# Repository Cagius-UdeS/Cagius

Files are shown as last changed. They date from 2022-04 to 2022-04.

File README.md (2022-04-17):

# Cagius

Cagius est un projet open source ayant pour objectif de concevoir et construire le mécanisme de gestion de la litière pour une cage à petits animaux automatisée et créer un interface programmable pour gérer les cycles de nettoyage.

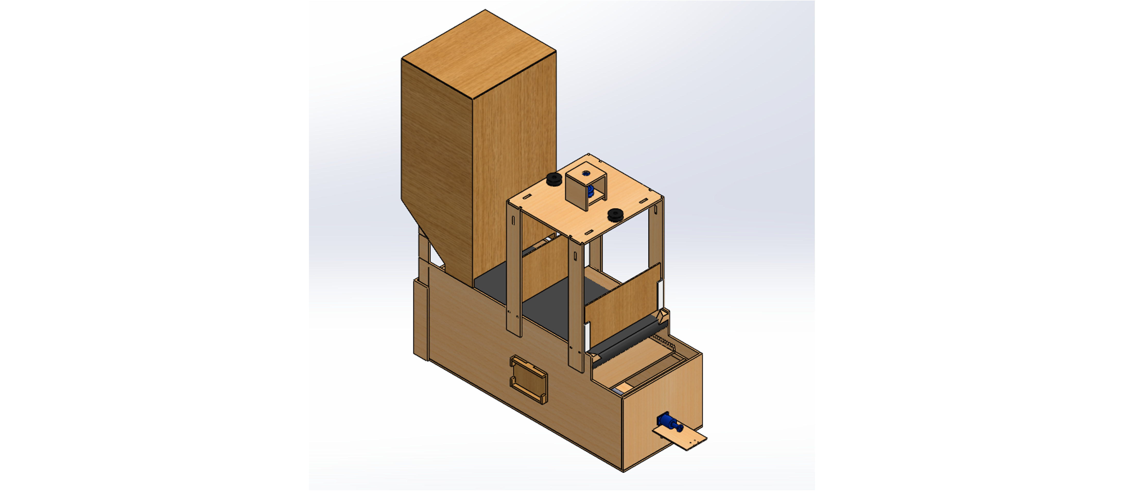
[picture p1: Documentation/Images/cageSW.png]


## Table des matieres

1. [Composantes mécaniques et électroniques](#1-composantes-mécaniques-et-électroniques)
2. [Assemblage](#2-assemblage)
3. [Installation logiciel](#3-installation-logiciel)
4. [Initialisation de la cage](#4-initialisation-de-la-cage)
5. [License](#5-license)

## 1. Composantes mécaniques et électroniques

### 1.1 Composantes mécaniques

- Courroie Synchrone : McMaster **1679K55** 
- Tige Filletée : Mcmaster **98957A154**

### 1.2 Composantes électroniques

- Raspberry Pi 4
- Raspberry Pi Camera
- 2 x Dynamixel XL-430-w250-t
- 2 x Dynamixel XM-430-w350-t
- Module à relais IDUINO - 1 Canal - 5V (ST1080)

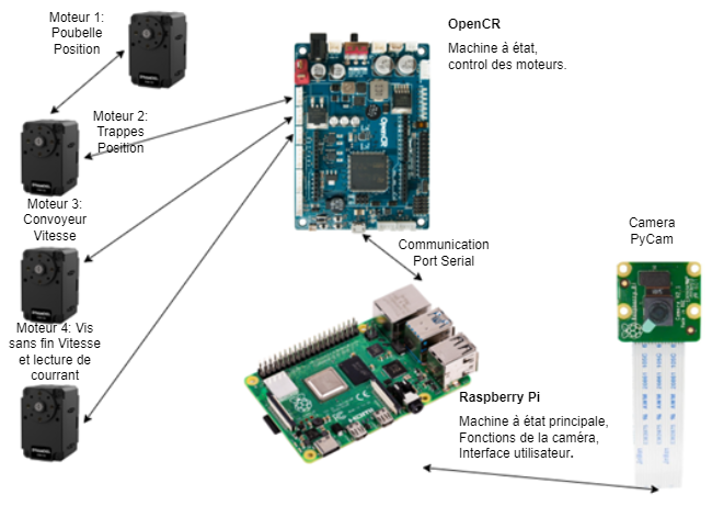
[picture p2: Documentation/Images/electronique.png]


## 2. Assemblage

Pour ce qui est de l'assemblage de la structure de base, il suffit de respecter l'assemblage de la pièce [Poubelle.sldrpt](https://github.com/Cagius-UdeS/Cagius/blob/main/CADs/Poubelle.SLDPRT). En fait, un mélange de colle et de clou à finition a été utilisé pour avoir une structure solide. De plus, le prototype actuelle est fait avec des planches de bois 1/4" découpées au laser et assemblées par la suite.

Pour ce qui est de l'assemblage du convoyeur, des tubes de PVC de 1" ont été utilisé, accompagnés d'adaptateurs imprimés en 3D pour les assembler avec la cage et le moteur. De plus, des bandes élastiques d'entrainements sont utilisées comme courroie pour transmettre le mouvement d'une poulie à l'autre.

[Pour les détails concernants les CADs et leurs pertinences](https://github.com/Cagius-UdeS/Cagius/blob/main/Documentation/Hierarchie_pieces.md)

## 3. Installation logiciel

La section suivante couvre l'installation des logiciels et des librairies nécessaires à la compilation du code.

### 3.1 Installation sur ordinateur

Il est nécessaire de compiler et d'envoyer le code à la carte OpenCR à partir d'un ordinateur, car le Raspberry Pi ne prend pas en charge les librairies de la carte OpenCR et des moteurs Dynamixel.

#### 3.1.1 Installation de Arduino IDE

Afin d'installer Arduino IDE et les librairies nécessaires pour coder les moteurs, il suffit de suivre les étapes suivantes :

1. Télécharger l'application Arduino IDE [ici](https://www.arduino.cc/en/software)
2. Ouvrir l'application et se rendre dans *Fichier*, puis *Préférences*
3. Dans la section *URL de gestionnaire de cartes supplémentaires*, rajouter la ligne suivante:
	`https://raw.githubusercontent.com/ROBOTIS-GIT/OpenCR/master/arduino/opencr_release/package_opencr_index.json`
4. Confirmer les changements en pressant *OK* dans le bas à droite de l'écran.
5. Enfin, installer les librairies Motorcontrole dans la section *Outils* puis *Type de carte* et *Gestionnaire de carte*. Taper OpenCR dans la barre de recherche et installer les librairies.

#### 3.1.2 Installation des librairies pour OpenCR

Afin de pouvoir compiler le code de la carte OpenCR, il est nécessaire d'installer quelques librairies selon les étapes suivantes :

1. Ouvrir l'application Arduino IDE et se rendre dans *Croquis*, puis *Inclure une bibliothèque* et sélectionner *Gestionnaires de bibliothèques*

2. Rentrer *Dynamixel* dans la barre de recherche

3. Installer les libraires

### 3.2 Installation sur Raspberry Pi

Le Raspberry Pi agit comme le cerveau de la cage. En effet, le Raspberry Pi analyse la caméra et l'interface utilisateur.

#### 3.2.1 Installation de Qt designer

Si vous voulez modifier l'interface utilisateur (modifier les fichiers .ui), vous devez télécharger Qt 5 Designer, qui fait parti de Qt Creator. Pour cela, éxecutez les lignes de commandes suivantes dans le terminal :

  ```
  $ sudo apt-get install qttools5-dev-tools
  $ sudo apt-get install qttools5-dev
  ```

#### 3.2.2 Installation de PyQt

Pour concevoir le HMI, nous avons utilisé PyQt qui est un module libre permettant de lier le langage Python avec la bibliothèque Qt. 
L'installation se fait sur le Raspberry Pi et consiste à faire rouler la ligne de commande suivante :

	$ sudo apt-get install python3-pyqt5

Si votre Rapsberry Pi n'est pas à jour, rouler ces lignes de commande au préalable :

	$ sudo apt-get update
	$ sudo apt-get upgrade

À partir de là, pour coder l'interphace graphique on utilise Qt 5 Designer avec le PyQt intégré.

#### 3.2.3 Installation des librairies Open CV

Afin d'installer les librairies OpenCV sur votre Raspberry Pi, 
il suffit de suivre le guide **Setting Up Open-CV for Object Detection** sur ce site:
[Guide d'installation OpenCV](https://core-electronics.com.au/tutorials/object-identify-raspberry-pi.html)

## 4. Initialisation de la cage

Les differents dossiers de code et où les compiler se retrouve [ici](Code/README.md).

Les étapes pour initialiser la cage et la lancer sont les suivantes :

- Remplir le réservoir de litière
- Si premier cycle d'utilisation, mettre une couche de litière sur le convoyeur
- S'assurer que la carte OpenCR, le Raspberry et les bandes LED sont alimentés
- S'assurer que la caméra est branchée sur le Raspberry Pi
- S'assurer que tous les moteurs sont branchés à la carte OpenCR
- Compiler le programme *[userInterface](Code/PyQt/userInterface.py)* sur le Raspberry Pi et attendre que l'initialisation soit complétée et que la fenêtre s'ouvre
- Indiquer le nombre d'animaux présents dans la cage, rentrer les heures d'activités souhaitées de la cage et appuyer sur le bouton **Lancement**
- La cage est prête à être utilisée !

<ins><b>Notez bien</b></ins> : Si jamais vous fermez la fenêtre de l'interface ou si vous souhaitez changez les paramètres rentrés initialement (nombre d'animaux, heures d'activités), il faut absolument désalimenter complétement la carte OpenCR et la réalimenter.

## 5. License

License de [Apache](LICENSE).

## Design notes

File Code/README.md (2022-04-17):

# Architechture générale du programme

Ce présent document explique de façon générale où doivent être compilés les fichiers du système.

1. [OpenCR](#1-opencr)
2. [Raspberry Pi](#2-raspberry-pi)
3. [Algorithme d'éxécution des séquences](#3-algorithme-déxécution-des-séquences)

## 1. OpenCR

Le programme contenu dans le dossier OpenCR/main doit etre compilé par un ordinateur sur Arduino IDE apres l'installation décrite [ici](../README.md/#311-installation-de-arduino-ide). Le code est défini [dans ce document ci](OpenCR/main/README.md).

## 2. Raspberry Pi

Le [programme](PyQt/userInterface.py) contenu dans le dossier PyQt doit être compilé sur le Raspberry Pi et celui-ci utilise les fichiers dans PiCamera et Main. L'installation du Rapberry Pi est décrite [ici](../README.md/#32-installation-sur-raspberry-pi). Le code est défini dans ces trois documents: [PyQt](PyQt/README.md), [Main](Main/README.md) et [PiCamera](PiCamera/README.md).

## 3. Algorithme d'éxécution des séquences

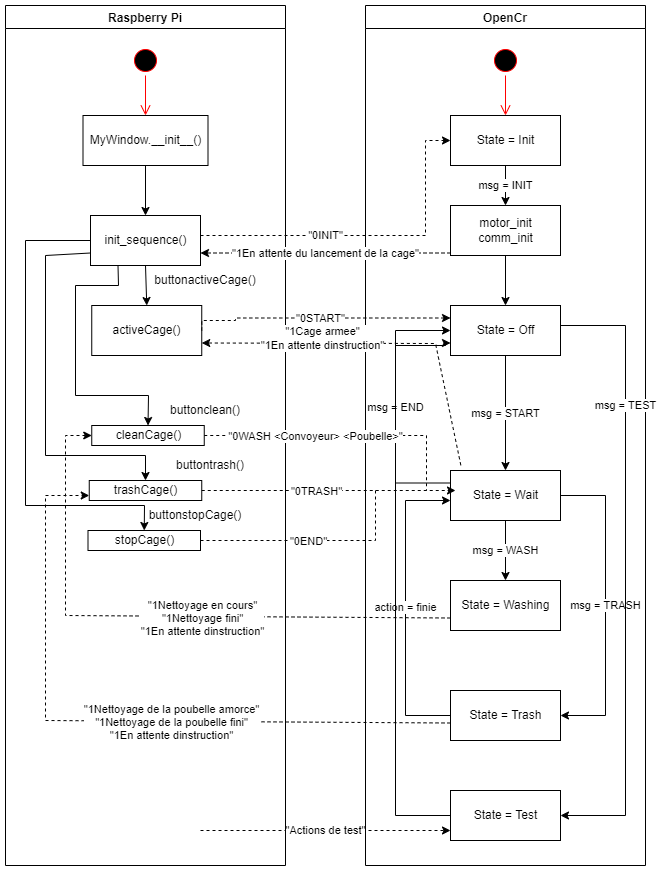
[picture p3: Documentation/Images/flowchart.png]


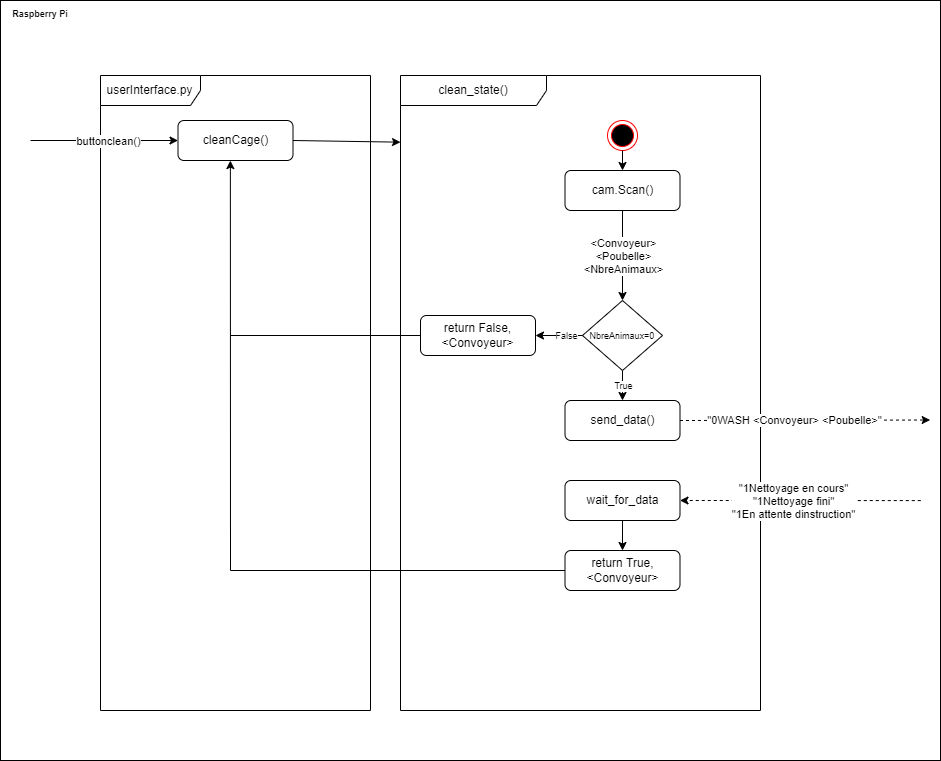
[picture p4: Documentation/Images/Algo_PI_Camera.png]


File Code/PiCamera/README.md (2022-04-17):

# Dossier *PiCamera*

Ce présent document comporte les détails paramétrables et les informations pertinentes sur la caméra.

1. [Supports](#1-supports)
2. [Étapes de calibration FishEye](#2-étapes-de-calibration-fisheye)
3. [Paramètres modifiables](#3-paramètres-modifiables)
4. [Valeurs de retour](#4-valeurs-de-retour)
5. [Algorithme de fonctionnement de la caméra](#5-algorithme-de-fonctionnement-de-la-caméra)

## 1. Supports

Si vous utilisez la même caméra que nous utilisons, c'est-a-dire la Raspberry Pi Camera Rev 2.2, vous pouver imprimer ce support en 3D afin de pouvoir fixer votre caméra au dessus de la litière :

- [Support Caméra](https://github.com/Cagius-UdeS/Cagius/blob/main/CADs/SupportCamera.SLDPRT)
- [Pied Caméra](https://github.com/Cagius-UdeS/Cagius/blob/main/CADs/PivotCamera.SLDPRT)

## 2. Étapes de calibration FishEye

1. Afin de calibrer la caméra, vous dever d'abord imprimer la [grille de calibration](https://github.com/Cagius-UdeS/Cagius/blob/main/Code/PiCamera/FECalibrationA4.png) et la coller sur une surface dure afin de pouvoir la manipuler sans que la feuille se plie.

2. Ensuite, il faut exécuter le code PatternCapture.py qui prend une photo toute les 3 secondes. Changer l'orientation et la position de la grille pour chacune des photo.

3. Une fois les photos prisent, exécuter le code CalibrationCam.py afin d'obtenir les variables de calibration de votre FishEye comme suit : .

4. Changer ensuite les valeurs présente dans la fonction undistort du code FonctionsCam.py.

## 3. Paramètres modifiables

### 3.1 Couleurs des zones

Puisque nous utilisons les couleurs afin de détecter tout ce que nous avons à détecter, la luminosité a beaucoup d'impact sur la réussite ou l'échec de la détection. Nous avons donc ajouté une bande DEL afin de rendre l'environnement stable. Par contre, si vous décidez d'utiliser des couleurs différentes ou si la luminosité extérieure a trop d'impact sur la couleur, il est possible de changer ces lignes de code afin de changer ou peaufiner les couleurs à détecter : 

### 3.2 Aires des zones

Il est aussi possible de changer les dimenssions des objets à trouver afin de filtrer les résidus involontaires. Pour ce faire, vous pouvez changer les valeurs suivantes pour augmenter ou diminuer l'aire des zones à trouver : 

### 3.3 Pourcentage des zones souillées pour vider

Cette valeurs permet de changer le seuil que les zones souillées doivent atteindre au total avant de nécéssité un vidage de la litière : 
 
## 4. Valeurs de retour

Ce code est une fonction que l'on peut appeller soit Scan() qui retourne la fraction sur 3 donc (0,1,2 ou 3) ainsi que le nombre de lapins présents dans la zone. Ne pas oublier d'ajouter la fonction InitGPIO afin d'activer les I/O du Raspberry Pi.

## 5. Algorithme de fonctionnement de la caméra

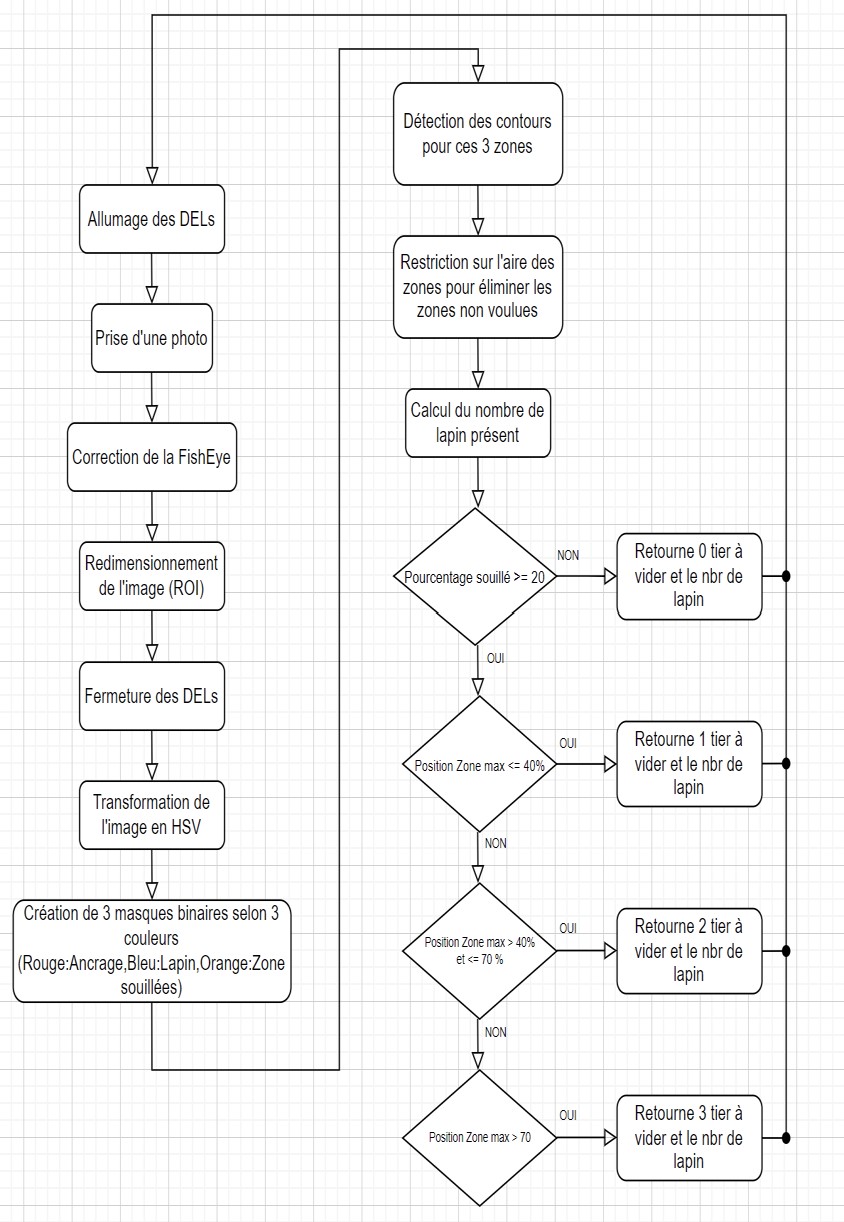
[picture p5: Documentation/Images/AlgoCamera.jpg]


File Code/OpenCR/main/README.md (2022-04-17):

# Dossier *OpenCR\main* 

Le présent document comporte les informations pertinentes sur le programme principal de la carte OpenCR et ses sous-programmes.

1. [Description des fichiers](#1-description-des-fichiers)
2. [Structure du programme](#2-structure-du-programme)
3. [Communication Pi et OpenCR](#3-communication-pi-et-opencr)

## 1. Description des fichiers

Le dossier main est celui à exécuter sur la carte Open CR à partir du logiciel Arduino IDE dont l'installation est expliquée [ici](../../../README.md/#311-installation-de-arduino-ide).

- **main.ino**: Fichier contenant la machine à état. Appelles les actions possibles, par exemple nettoyer la cage de *action_function.cpp*. Ce fichier appelle les fonctions de *action_functions.cpp* et *serialcomm_functions.cpp*.
- **serialcomm_functions.cpp**: Fichier contenant les fonctions de communications par port série avec le Rapsberry Pi.
- **motor_functions.cpp**: Fichier contenant les fonctions de mouvements des moteurs et des constantes touchant directement les moteurs, par exemple la vitesse, le délai, la position pour x nombre de tours. 
- **action_functions.cpp**: Fichier contenant les fonctions de nettoyages utilisant les moteurs et des constantes, les ID des moteurs, des positions et mouvements propres aux actions. Ces fonctions définissent les differents actions de la cage, par exemple ouvrir les trappes et partir le convoyeur. Les fonctions appellent les fonctions générales d'utilisation de moteurs (*motor_functions.cpp*). Ce fichier appelle les fonctions de *motor_functions.cpp*

### 1.1 Notes 

Lors de l'initialisation des moteurs dynamixel, s'assurer que tous les moteurs ont un ID different, le tout peut être possible grâce au code du fabricant retrouvé dans les exemples (p_monitor). 

## 2. Structure du programme

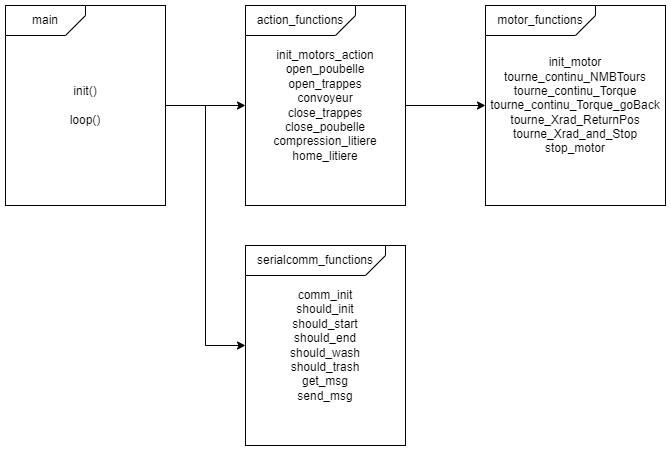
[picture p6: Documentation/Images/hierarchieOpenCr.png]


### 2.1 Structure de la séquence de nettoyage

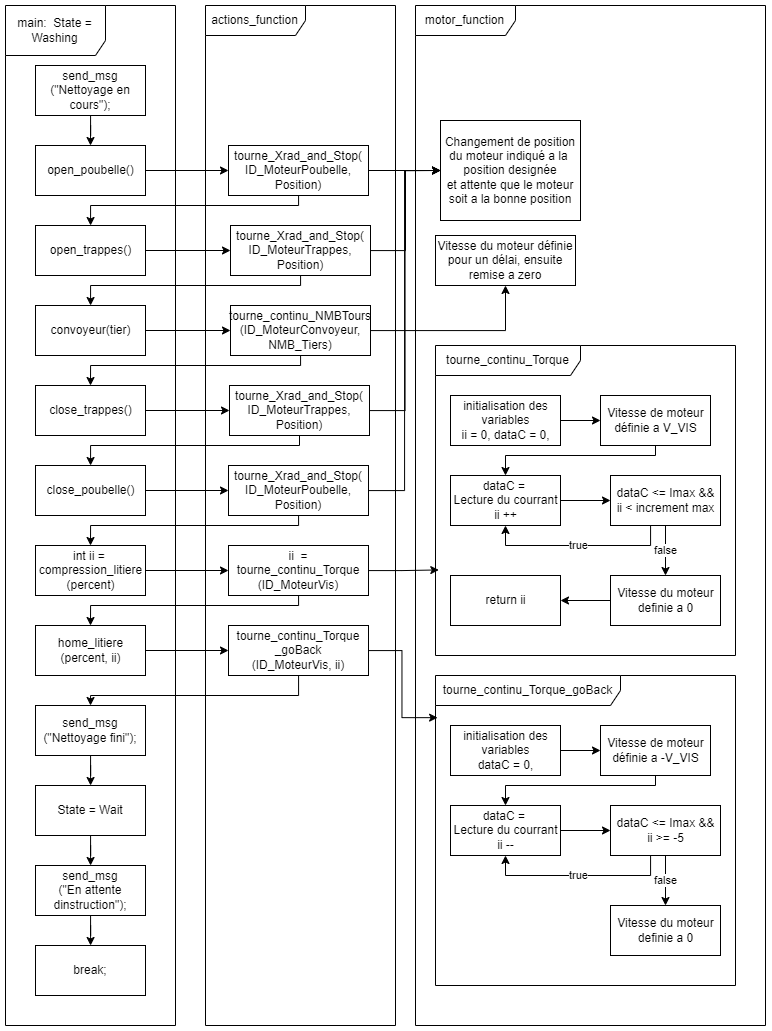
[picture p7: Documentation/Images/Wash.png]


## 3. Communication Pi et OpenCR

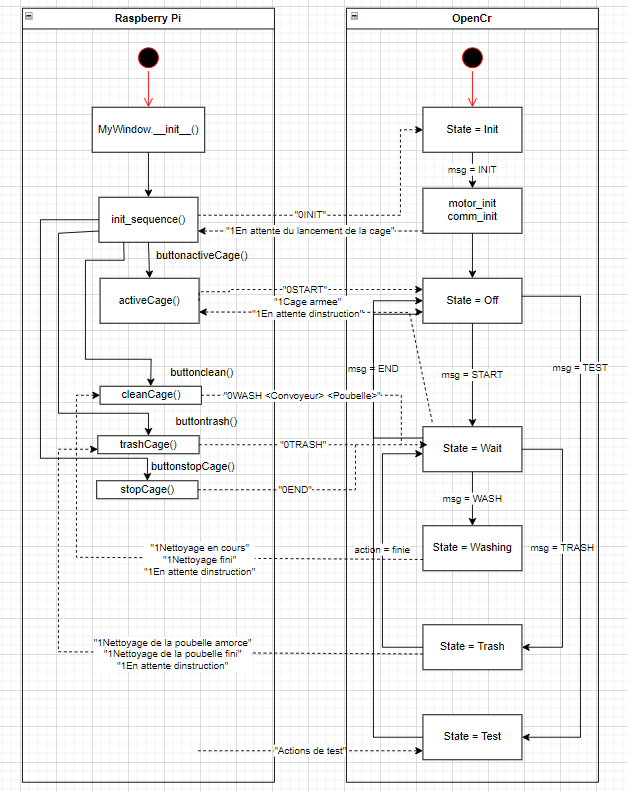
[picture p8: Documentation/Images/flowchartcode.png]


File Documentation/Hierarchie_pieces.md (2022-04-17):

Il est à noter que tous les DXF et PDF pour découper au laser les pièces sont disponibles dans le dossier [découpe laser](https://github.com/Cagius-UdeS/Cagius/tree/main/CADs/Laser%20cutting) et que la majorité des STL sont présents dans le dossier [CADs](https://github.com/Cagius-UdeS/Cagius/tree/main/CADs)

Voici la liste des pièces importantes pour l'assemblage de la poubelle :
- [Assemblage finale](https://github.com/Cagius-UdeS/Cagius/blob/main/CADs/Assemblage_finale.SLDASM)
- [Poubelle](https://github.com/Cagius-UdeS/Cagius/blob/main/CADs/Poubelle.SLDPRT)
- [Poulie et crémaillère](https://github.com/Cagius-UdeS/Cagius/tree/main/CADs/Poulie%20et%20cr%C3%A9maill%C3%A8re)
- [Vis sans fin](https://github.com/Cagius-UdeS/Cagius/tree/main/CADs/Vis%20sans%20fin)
- [Réserve de litière](https://github.com/Cagius-UdeS/Cagius/blob/main/CADs/Reserve_Litiere.SLDPRT)

Le reste des pièces présentes ne sont pas nécéssairement utiles pour la réalisation/assemblage de la cage automatisée ou sont montrées dans l'assemblage finale !

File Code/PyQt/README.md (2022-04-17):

# Dossier *PyQt*

Le présent document comporte des informations pertinentes sur l'interface utilisateur et ses programmes.

1. [Description des fichiers](#1-description-des-fichiers)
2. [Structure du programme](#2-structure-du-programme)
3. [Fenêtre principal de l'interface utilisateur](#3-fenêtre-principal-de-linterface-utilisateur)

## 1. Description des fichiers

Il y a deux types de fichiers dans ce dossier, des .py et des .ui. Les fichiers .ui peuvent être ouverts avec QT 5 Designer, dont l'installation est expliquée [ici](../../README.md/#321-installation-de-qt-designer), sur le Pi et les fichiers .py avec Visual Studio Code. 

- **mainWindow_geometry.py** : Fichier contenant la fenêtre principale du HMI en Python.
- **mainWindow_geometry.ui** : Fichier représentant graphiquement la fenêtre principale du HMI.
- **popup_geometry.py** : Fichier contenant la fenêtre pop-up (qui s'ouvre lorsque la poubelle doit être vidée) du HMI en Python.
- **popup_geometry.ui** : Fichier représentant graphiquement la fenêtre pop-up du HMI.
- **userInterface.py** : Fichier main gérant la communication entre l'interface graphique et les autres composantes du système et entre les fenêtres de l'interface.

### 1.1 Conversion des fichiers .ui en .py

Les fenêtres de l'interface utilisateur sont initialement conçues dans QT 5 Designer en fichier .ui. Enfin d'associer des actions aux différentes composantes de ces fenêtres, il faut convertir ces fichiers .ui en fichiers .py, et ce, en éxécutant la ligne de commande ci-dessous dans le dossier contenant les fichiers :

```
  $ pyuic5 –x nom.ui -o nom.py 
```

## 2. Structure du programme

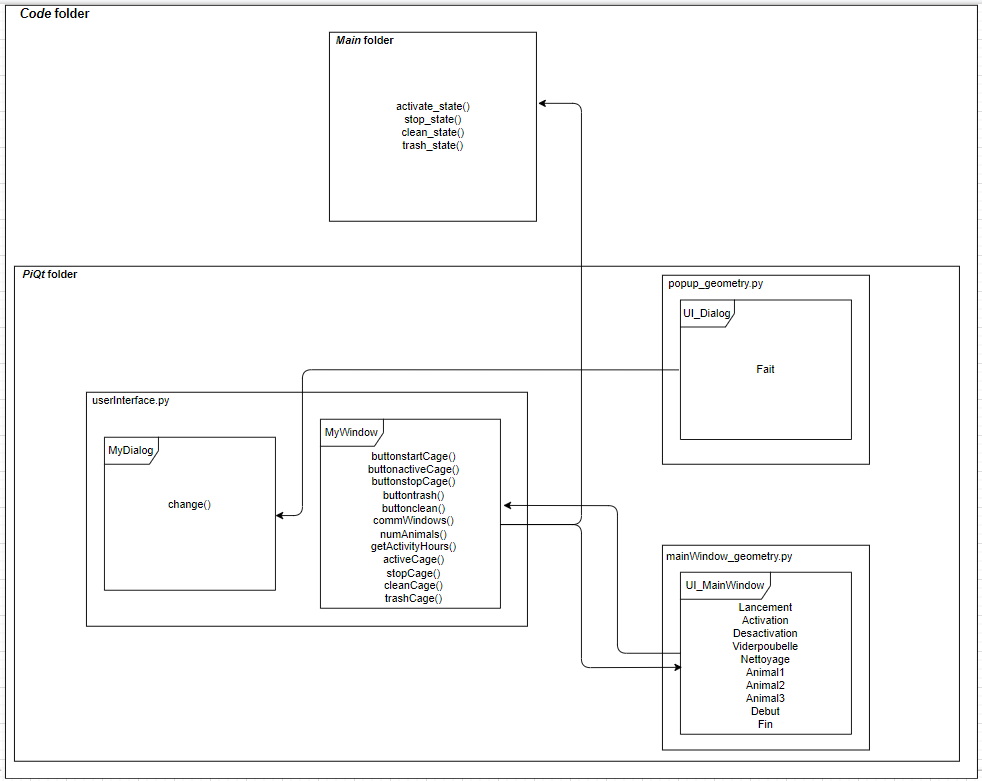
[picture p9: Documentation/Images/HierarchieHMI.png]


## 3. Fenêtre principal de l'interface utilisateur

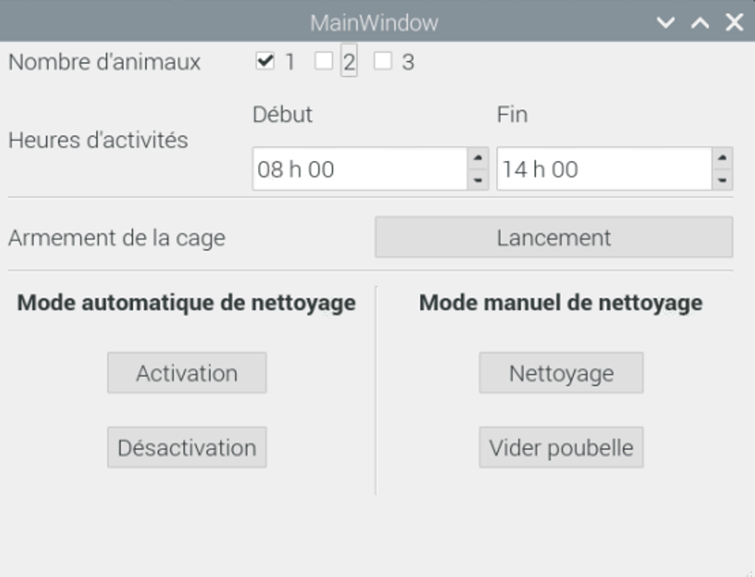
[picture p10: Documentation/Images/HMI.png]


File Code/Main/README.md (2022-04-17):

# Dossier *Main*

Ce présent document comporte les informations pertinentes sur les fichiers main du système.

1. [Descriptions des fichiers](#1-description-des-fichiers)
2. [Structure du programme](#2-structure-du-programme)

## 1. Description des fichiers

Les fichiers de ce dossier assurent la communication entre le Raspberry Pi, la carte OpenCR et la caméra Pi et contiennent la machine à état générale du code, en d'autres termes la séquence d'éxécution.

- **functions_Comm** : Fichier contenant les différentes fonctions pour envoyer, recevoir et attendre des messages de la carte OpenCR.
- **init_stop_Sequences** : Fichier contenant les différentes fonctions d'initialisation de composantes ou de séquence, de lancements d'états.

## 2. Structure du programme

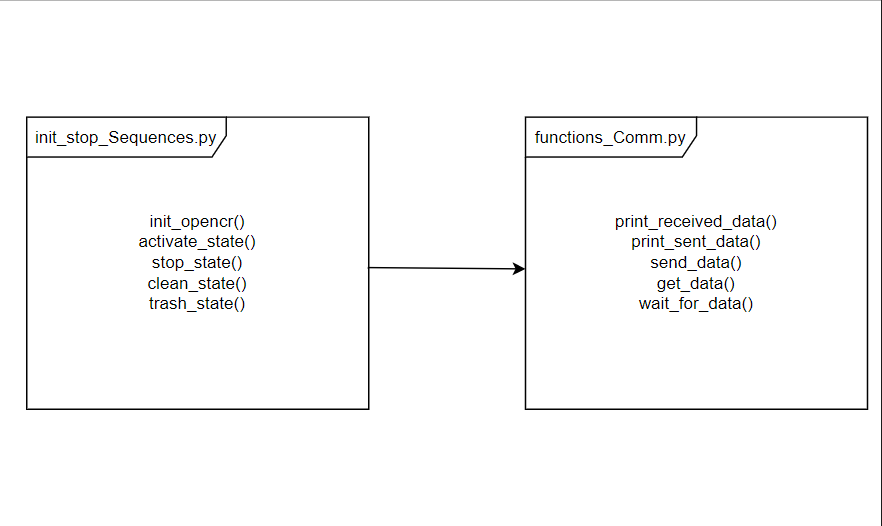
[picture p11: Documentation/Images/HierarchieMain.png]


### 2.1 Communication Pi et OpenCR



### 2.2 Algorithme d'utilisation de la caméra dans la séquence



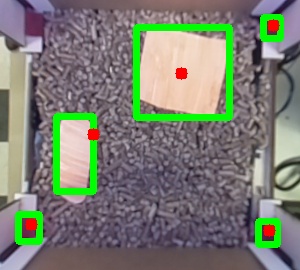
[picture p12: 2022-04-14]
Code/LitiereContours.jpg

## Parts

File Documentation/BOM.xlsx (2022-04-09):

BILL OF MATERIALS
 |  | Objet à créer : | Litière automatisé pour petit animaux
 |  | Qty à créer : | 1
COMPOSANT | # MODÈLE | DESCRIPTION | QTY DE BASE | COÛT PAR UNITÉ | SOUS-TOTAL | Hyper lien
Vis sans fin | Mcmaster 98957A154 | Mécanisme de la litière | 1 | 1.50 $ | 1.50 $
Moteur |  | Dynamixel XM430-w350-t | 2 | 0.00 $ | 0.00 $
Moteur |  | Dynamixel XL430-w250-t | 2 | 0.00 $ | 0.00 $
Courroies | Rossy | Bande élastique d'entrainement - Mécanisme convoyeur | 2 | 8.00 $ | 16.00 $
Rouleaux | 1¼' de diamètre | Tuyau de PVC - Mécanisme convoyeur | 1 | 0.00 $ | 0.00 $
Bois | Feuille de bois 1/4" merisier 4' x 8' | Structure mécanique | 1 | 0.00 $ | 0.00 $
Bois | Panneau de bois 1/8" agglomeres 4' x 4' | Structure mécanique | 1 | 6.62 $ | 6.62 $
Bois | Quart de rond peint 11/16" Pin | Structure mécanique | 2 | 3.09 $ | 6.18 $
Caméra | RaspberryPi Camera Rev 2.2 | Caméra | 1 | 0.00 $ | 0.00 $
Carte OpenCR |  |  | 1 | 0.00 $ | 0.00 $
Raspberry Pi |  |  | 1 | 0.00 $ | 0.00 $
Relais DC | SSRNC-430B | Contrôle les lumières de la caméra (12V) | 1 | 0.00 $ | 0.00 $
Strap lumières DEL |  | Éclairage du convoyeur - coupé en 4 | 1 | 0.00 $ | 0.00 $
Sac à poubelle | Type Résistant - Grandeur large | Tapis du convoyeur | 1 | 0.25 $ | 0.25 $
Poulie | Impression 3D | Mécanisme des trappes | 2 | 0.00 $ | 0.00 $
Poulie-moteur | Impression 3D | Mécanisme des trappes | 1 | 0.00 $ | 0.00 $
Adaptateur rouleau-structure | Impression 3D | Mécanisme du convoyeur | 3 | 0.00 $ | 0.00 $
Adaptateur rouleau-moteur | Impression 3D | Mécanisme du convoyeur | 1 | 0.00 $ | 0.00 $
Assemblage support | Impression 3D | Caméra | 1 | 0.00 $ | 0.00 $
Pivot caméra | Impression 3D | Caméra | 1 | 0.00 $ | 0.00 $
Coupleur de la vis sans fin | Impression 3D | Mécanisme de la litière | 1 | 0.00 $ | 0.00 $
Support début vis sans fin | Impression 3D | Mécanisme de la litière | 1 | 0.00 $ | 0.00 $
Support fin vis sans fin | Impression 3D | Mécanisme de la litière | 1 | 0.00 $ | 0.00 $
Support plaque vis sans fin droit | Impression 3D | Mécanisme de la litière | 1 | 0.00 $ | 0.00 $
Support plaque vis sans fin gauche | Impression 3D | Mécanisme de la litière | 1 | 0.00 $ | 0.00 $
Adaptateur vis sans fin - moteur | Impression 3D | Mécanisme de la litière | 1 | 0.00 $ | 0.00 $
 |  |  | COÛT TOTAL: | $30.55

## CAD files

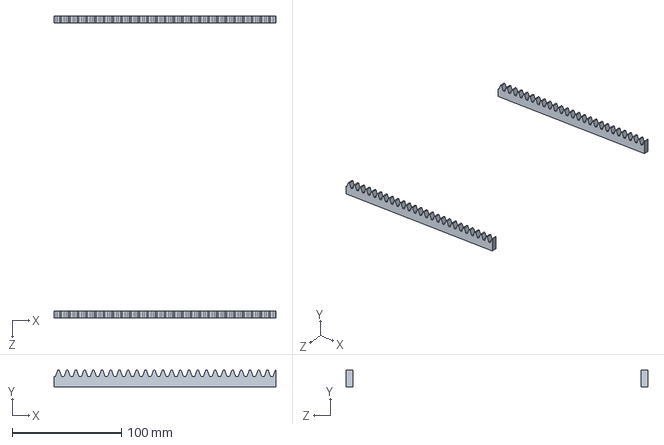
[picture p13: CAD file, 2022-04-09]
CADs/Poulie et crémaillère/poulie_cremaillere.SLDASM
203.2 x 15.2 x 276.9 mm
Inch - Rack-spur - rectangular 10DP 20PA 0.25FW 0.5PH 8L---SAll x 2

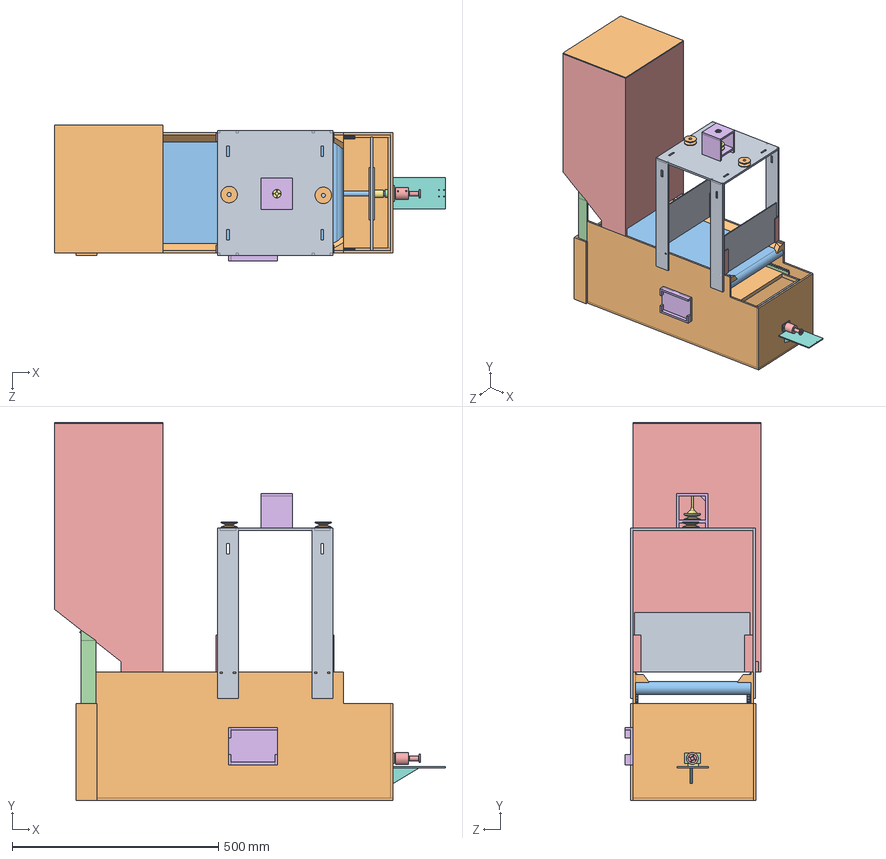
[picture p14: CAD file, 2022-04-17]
CADs/Assemblage_finale.SLDASM
947.2 x 916.3 x 329.0 mm
SupportsDessusCage
PoubelleV3_1_4po
Inch - Spur gear 10DP 15T 20PA 0.25FW ---S15N3.0H2.0L0.375N x 2
Inch - Rack-spur - rectangular 10DP 20PA 0.25FW 0.5PH 8L---SAll x 2
Support_trappes x 4
support_poulie_trappe
Poulie_moteur
Support_mot_vis_sans_fin
Trape x 2
Poulie x 2
vis_sans_fin
support_reservoir
Reserve_Litiere
Support_carte_OpenCR
vis_sans_fin_moteur_1de2
vis_sans_fin_moteur_2de2
vis_sans_fin_plaque
Couvercle_reservoir
Convoyeur
vis_sans_fin_support_debut
Coupleur_screw

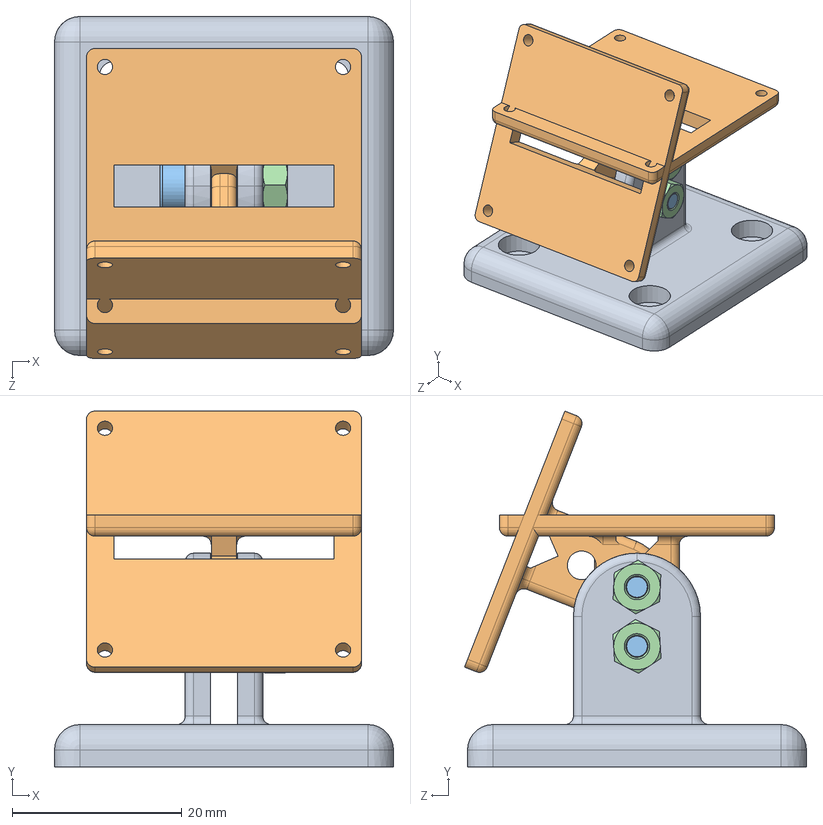
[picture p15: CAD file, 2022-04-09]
CADs/CameraAssem.SLDASM
40.0 x 42.0 x 40.4 mm
PivotCamera
SupportCamera x 2
socket head cap screw_am x 2
hex nut style 2_am x 2

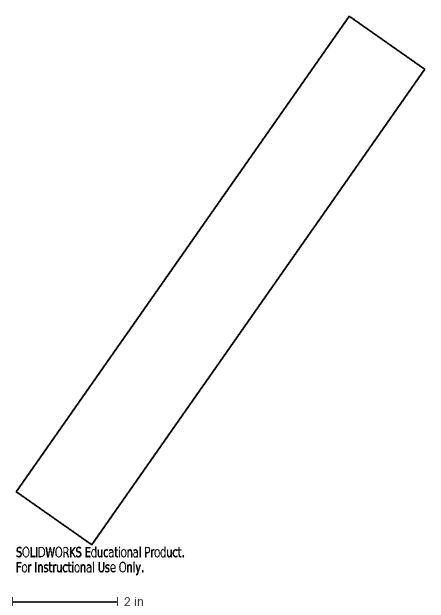
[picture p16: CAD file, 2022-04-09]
CADs/Laser cutting/DXF/support_reservoir_largeur.DXF
SOLIDWORKS Educational Product.
For Instructional Use Only.

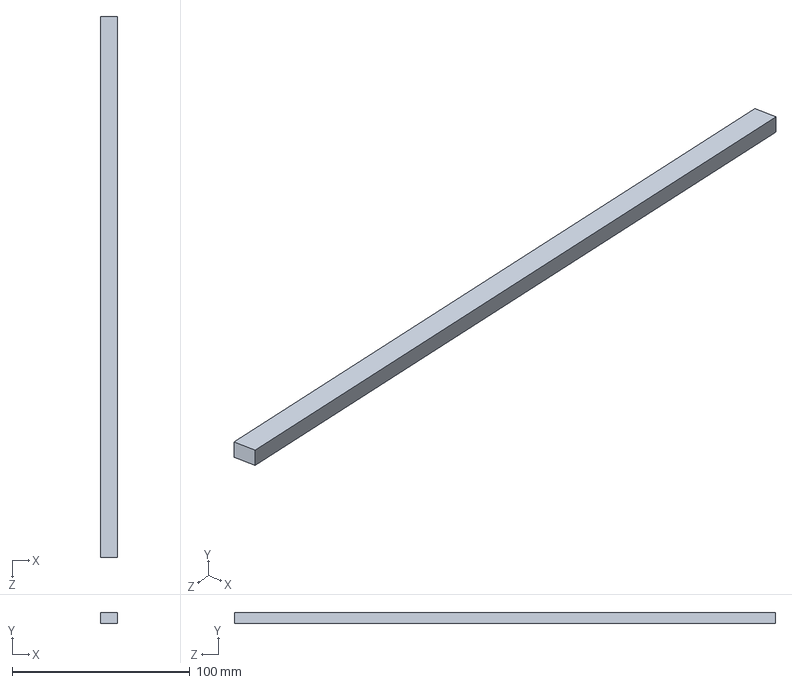
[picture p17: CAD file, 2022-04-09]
CADs/Poulie et crémaillère/poulie_cremaillere_Tige_2de3.SLDPRT
9.65 x 6.35 x 304.8 mm

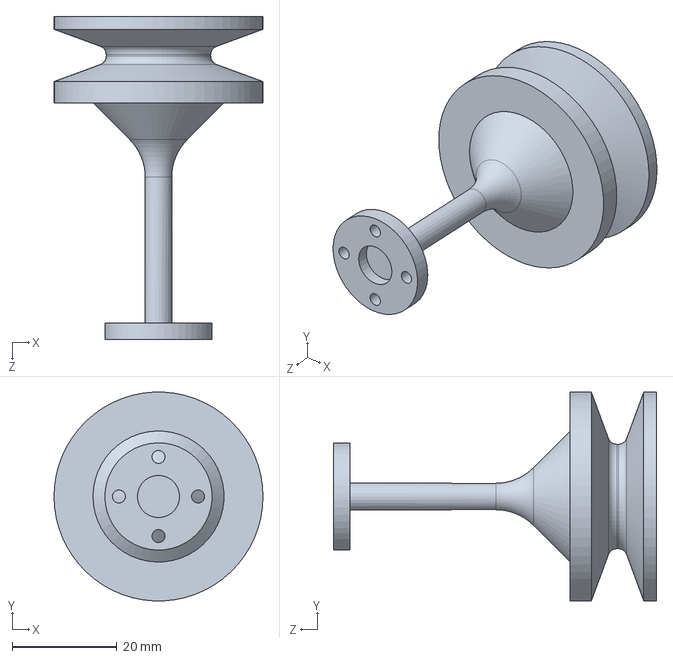
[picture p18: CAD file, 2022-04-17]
CADs/Poulie_moteur.SLDPRT
40.0 x 39.9 x 61.9 mm

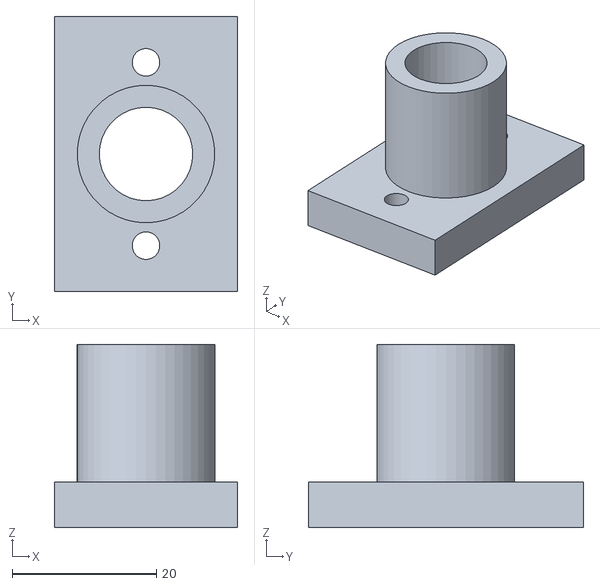
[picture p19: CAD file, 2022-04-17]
CADs/STL/vis_sans_fin_support.STL
25.4 x 38.1 x 25.4

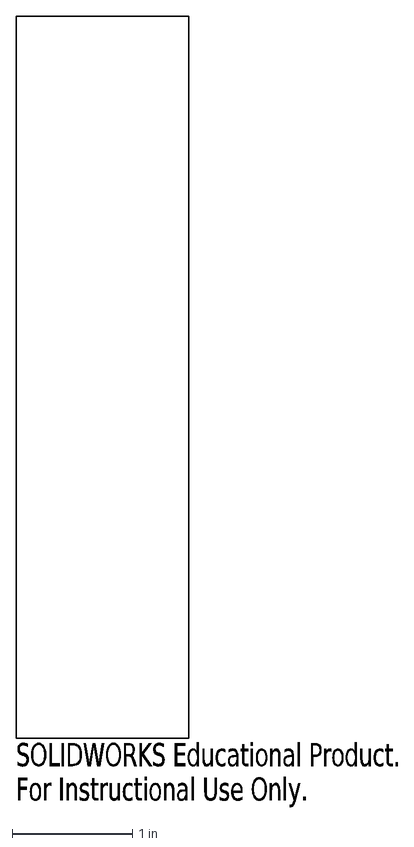
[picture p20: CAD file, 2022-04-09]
CADs/Laser cutting/DXF/support_reservoir_hauteur.DXF
SOLIDWORKS Educational Product.
For Instructional Use Only.

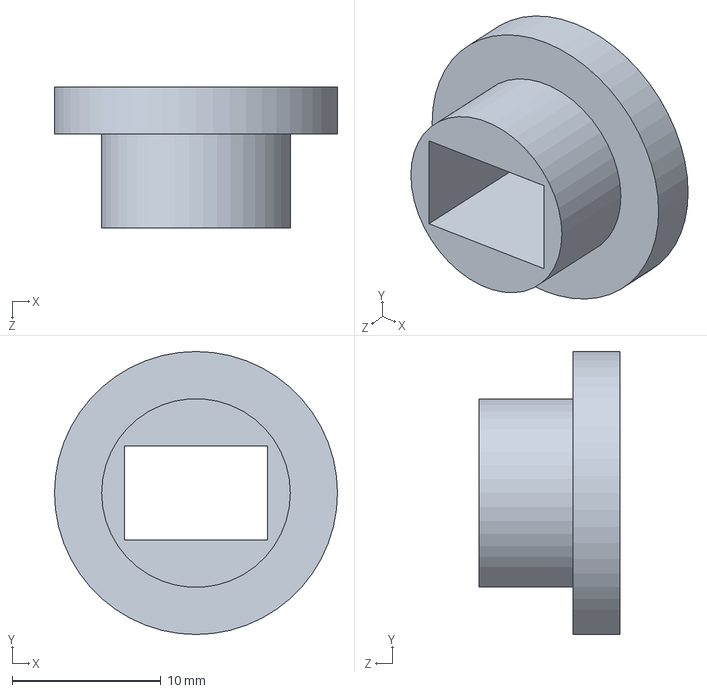
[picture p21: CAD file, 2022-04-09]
CADs/Poulie et crémaillère/poulie_cremaillere_Tige_3de3.SLDPRT
19.1 x 19.1 x 9.52 mm

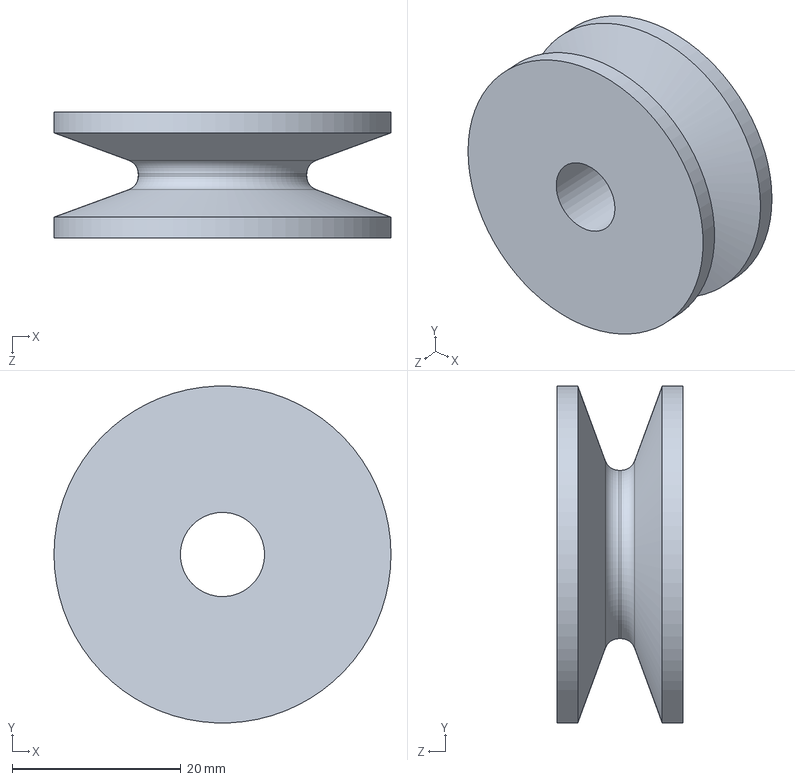
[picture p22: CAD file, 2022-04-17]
CADs/Poulie.SLDPRT
40.0 x 40.0 x 15.0 mm

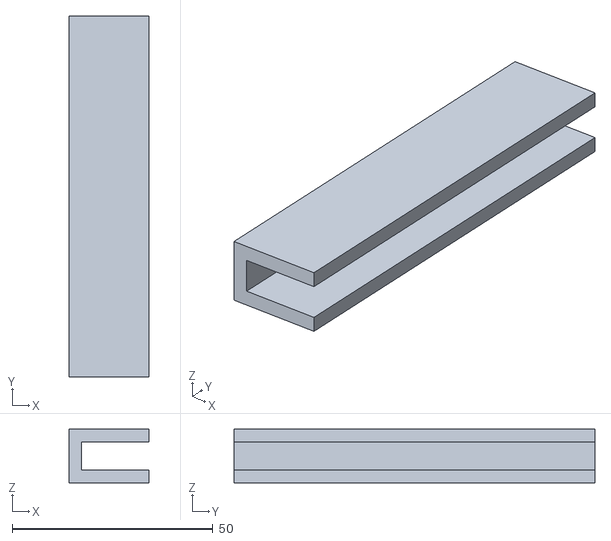
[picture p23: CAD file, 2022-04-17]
CADs/STL/Support_trappes.STL
20.0 x 90.0 x 13.3

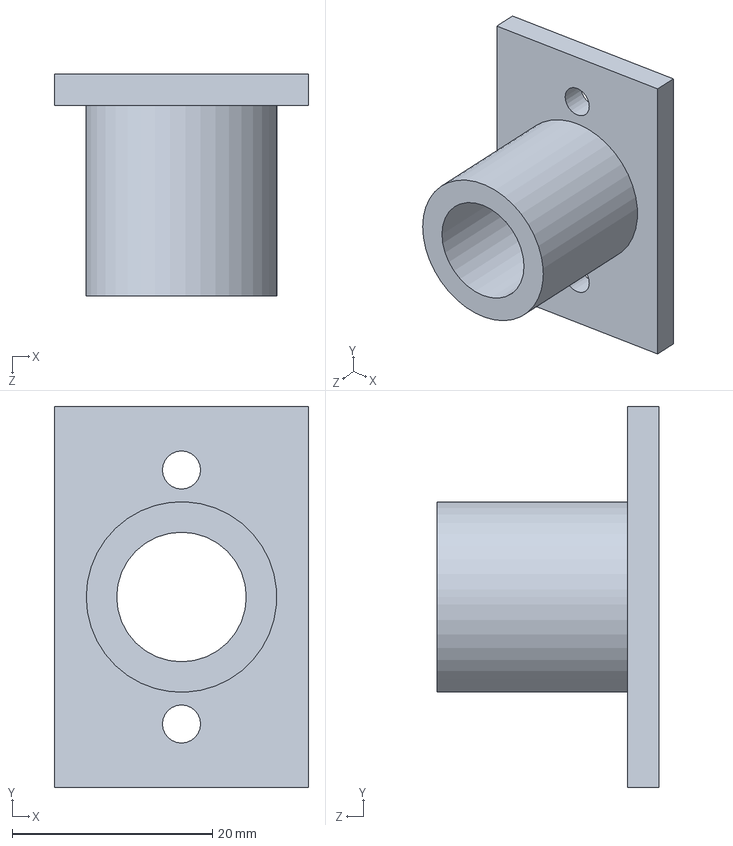
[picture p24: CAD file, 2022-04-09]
CADs/Vis sans fin/vis_sans_fin_support_debut.SLDPRT
25.4 x 38.1 x 22.2 mm

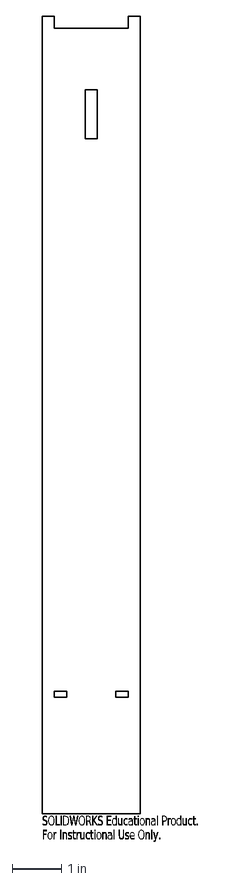
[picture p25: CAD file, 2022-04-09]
CADs/Laser cutting/DXF/PatteDessusCage.DXF
SOLIDWORKS Educational Product.
For Instructional Use Only.

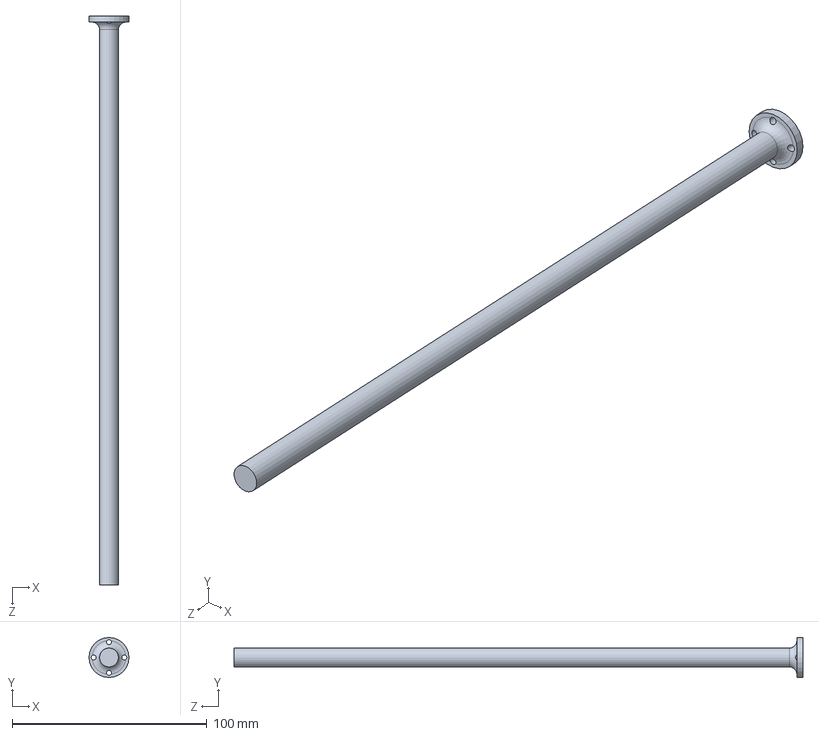
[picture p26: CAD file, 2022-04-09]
CADs/Poulie et crémaillère/poulie_cremaillere_Tige.SLDPRT
20.6 x 20.6 x 292.1 mm

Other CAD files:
CADs/STL/vis_sans_fin_moteur_2de2.STL
CADs/SupportsDessusCage.SLDPRT
CADs/Vis sans fin/vis_sans_fin_plaque.SLDPRT
CADs/Convoyeur.SLDPRT
CADs/Drawing/Mise en plan.SLDDRW
CADs/Drawing/Mise en plan2.SLDDRW
CADs/Laser cutting/DXF/AncrageCalibration.DXF
CADs/Laser cutting/DXF/Support_mot_trappe_poubelle.DXF
CADs/Laser cutting/DXF/Support_mot_vis_sans_fin.DXF
CADs/Laser cutting/DXF/Support_mot_vis_sans_fin_triangle.DXF
CADs/Laser cutting/DXF/SupportsDessusCage.DXF
CADs/Laser cutting/DXF/arrière_11_5po.DXF
CADs/Laser cutting/DXF/avant_arrière.DXF
CADs/Laser cutting/DXF/coté.DXF
CADs/Laser cutting/DXF/fond.DXF
CADs/Laser cutting/DXF/gear.DXF
CADs/Laser cutting/DXF/languette_arrière_large.DXF
CADs/Laser cutting/DXF/languette_arrière_petite.DXF
CADs/Laser cutting/DXF/planche_millieu.DXF
CADs/Laser cutting/DXF/plaque_convoyeur.DXF
CADs/Laser cutting/DXF/poulie_cremaillere_Tige_2de3.DXF
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

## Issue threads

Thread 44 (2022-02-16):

Assemblage du rouleau fixe avec le moteur

LaurieUDES, 2022-02-16:

Closed 2022-03-23.

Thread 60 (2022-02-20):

Documentation mecanique

florencemillette, 2022-02-20:

florencemillette, 2022-02-20:
explication de l'assemblage, un README avec tout l'explication et un lien vers celui ci de maniere logique (amusez vous faites comme vous voulez) a partir du readme principal

Closed 2022-02-22.

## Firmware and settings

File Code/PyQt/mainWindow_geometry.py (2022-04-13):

# -*- coding: utf-8 -*-

# Form implementation generated from reading ui file 'mainWindow_geometry.ui'
#
# Created by: PyQt5 UI code generator 5.11.3
#
# WARNING! All changes made in this file will be lost!

from PyQt5 import QtCore, QtGui, QtWidgets

class Ui_MainWindow(object):
    def setupUi(self, MainWindow):
        MainWindow.setObjectName("MainWindow")
        MainWindow.resize(618, 446)
        self.centralwidget = QtWidgets.QWidget(MainWindow)
        self.centralwidget.setObjectName("centralwidget")
        self.gridLayoutWidget = QtWidgets.QWidget(self.centralwidget)
        self.gridLayoutWidget.setGeometry(QtCore.QRect(10, 0, 591, 122))
        self.gridLayoutWidget.setObjectName("gridLayoutWidget")
        self.gridLayout = QtWidgets.QGridLayout(self.gridLayoutWidget)
        self.gridLayout.setContentsMargins(0, 0, 0, 0)
        self.gridLayout.setObjectName("gridLayout")
        self.gridLayout_7 = QtWidgets.QGridLayout()
        self.gridLayout_7.setObjectName("gridLayout_7")
        self.Fin = QtWidgets.QTimeEdit(self.gridLayoutWidget)
        self.Fin.setObjectName("Fin")
        self.gridLayout_7.addWidget(self.Fin, 2, 2, 1, 1)
        self.label_3 = QtWidgets.QLabel(self.gridLayoutWidget)
        self.label_3.setObjectName("label_3")
        self.gridLayout_7.addWidget(self.label_3, 0, 0, 1, 1)
        self.label_4 = QtWidgets.QLabel(self.gridLayoutWidget)
        self.label_4.setObjectName("label_4")
        self.gridLayout_7.addWidget(self.label_4, 1, 0, 2, 1)
        self.label_5 = QtWidgets.QLabel(self.gridLayoutWidget)
        self.label_5.setObjectName("label_5")
        self.gridLayout_7.addWidget(self.label_5, 1, 1, 1, 1)
        self.label_6 = QtWidgets.QLabel(self.gridLayoutWidget)
        self.label_6.setObjectName("label_6")
        self.gridLayout_7.addWidget(self.label_6, 1, 2, 1, 1)
        self.Debut = QtWidgets.QTimeEdit(self.gridLayoutWidget)
        self.Debut.setObjectName("Debut")
        self.gridLayout_7.addWidget(self.Debut, 2, 1, 1, 1)
        self.gridLayout_9 = QtWidgets.QGridLayout()
        self.gridLayout_9.setObjectName("gridLayout_9")
        self.horizontalLayout_2 = QtWidgets.QHBoxLayout()
        self.horizontalLayout_2.setObjectName("horizontalLayout_2")
        self.Animal1 = QtWidgets.QCheckBox(self.gridLayoutWidget)
        self.Animal1.setObjectName("Animal1")
        self.horizontalLayout_2.addWidget(self.Animal1)
        self.Animal2 = QtWidgets.QCheckBox(self.gridLayoutWidget)
        self.Animal2.setObjectName("Animal2")
        self.horizontalLayout_2.addWidget(self.Animal2)
        self.Animal3 = QtWidgets.QCheckBox(self.gridLayoutWidget)
        self.Animal3.setObjectName("Animal3")
        self.horizontalLayout_2.addWidget(self.Animal3)
        spacerItem = QtWidgets.QSpacerItem(40, 20, QtWidgets.QSizePolicy.Expanding, QtWidgets.QSizePolicy.Minimum)
        self.horizontalLayout_2.addItem(spacerItem)
        self.gridLayout_9.addLayout(self.horizontalLayout_2, 1, 0, 1, 1)
        self.gridLayout_7.addLayout(self.gridLayout_9, 0, 1, 1, 2)
        self.gridLayout.addLayout(self.gridLayout_7, 0, 0, 1, 1)
        self.gridLayoutWidget_5 = QtWidgets.QWidget(self.centralwidget)
        self.gridLayoutWidget_5.setGeometry(QtCore.QRect(320, 200, 281, 171))
        self.gridLayoutWidget_5.setObjectName("gridLayoutWidget_5")
        self.gridLayout_6 = QtWidgets.QGridLayout(self.gridLayoutWidget_5)
        self.gridLayout_6.setContentsMargins(0, 0, 0, 0)
        self.gridLayout_6.setObjectName("gridLayout_6")
        spacerItem1 = QtWidgets.QSpacerItem(20, 40, QtWidgets.QSizePolicy.Minimum, QtWidgets.QSizePolicy.Expanding)
        self.gridLayout_6.addItem(spacerItem1, 5, 1, 1, 1)
        self.Viderpoubelle = QtWidgets.QPushButton(self.gridLayoutWidget_5)
        self.Viderpoubelle.setObjectName("Viderpoubelle")
        self.gridLayout_6.addWidget(self.Viderpoubelle, 4, 1, 1, 1)
        spacerItem2 = QtWidgets.QSpacerItem(20, 40, QtWidgets.QSizePolicy.Minimum, QtWidgets.QSizePolicy.Expanding)
        self.gridLayout_6.addItem(spacerItem2, 1, 1, 1, 1)
        spacerItem3 = QtWidgets.QSpacerItem(40, 20, QtWidgets.QSizePolicy.Expanding, QtWidgets.QSizePolicy.Minimum)
        self.gridLayout_6.addItem(spacerItem3, 3, 2, 1, 1)
        spacerItem4 = QtWidgets.QSpacerItem(40, 20, QtWidgets.QSizePolicy.Expanding, QtWidgets.QSizePolicy.Minimum)
        self.gridLayout_6.addItem(spacerItem4, 3, 0, 1, 1)
        self.Nettoyage = QtWidgets.QPushButton(self.gridLayoutWidget_5)
        self.Nettoyage.setObjectName("Nettoyage")
        self.gridLayout_6.addWidget(self.Nettoyage, 2, 1, 1, 1)
        self.label_2 = QtWidgets.QLabel(self.gridLayoutWidget_5)
        font = QtGui.QFont()
        font.setBold(True)
        font.setWeight(75)
        self.label_2.setFont(font)
        self.label_2.setAlignment(QtCore.Qt.AlignCenter)
        self.label_2.setObjectName("label_2")
        self.gridLayout_6.addWidget(self.label_2, 0, 0, 1, 3)
        spacerItem5 = QtWidgets.QSpacerItem(20, 40, QtWidgets.QSizePolicy.Minimum, QtWidgets.QSizePolicy.Expanding)
        self.gridLayout_6.addItem(spacerItem5, 3, 1, 1, 1)
        self.line_2 = QtWidgets.QFrame(self.centralwidget)
        self.line_2.setGeometry(QtCore.QRect(300, 200, 20, 171))
        self.line_2.setFrameShape(QtWidgets.QFrame.VLine)
        self.line_2.setFrameShadow(QtWidgets.QFrame.Sunken)
        self.line_2.setObjectName("line_2")
        self.layoutWidget = QtWidgets.QWidget(self.centralwidget)
        self.layoutWidget.setGeometry(QtCore.QRect(10, 200, 291, 171))
        self.layoutWidget.setObjectName("layoutWidget")
        self.gridLayout_8 = QtWidgets.QGridLayout(self.layoutWidget)
        self.gridLayout_8.setContentsMargins(0, 0, 0, 0)
        self.gridLayout_8.setObjectName("gridLayout_8")
        self.Desactivation = QtWidgets.QPushButton(self.layoutWidget)
        self.Desactivation.setObjectName("Desactivation")
        self.gridLayout_8.addWidget(self.Desactivation, 4, 1, 1, 1)
        spacerItem6 = QtWidgets.QSpacerItem(20, 40, QtWidgets.QSizePolicy.Minimum, QtWidgets.QSizePolicy.Expanding)
        self.gridLayout_8.addItem(spacerItem6, 1, 1, 1, 1)
        spacerItem7 = QtWidgets.QSpacerItem(20, 40, QtWidgets.QSizePolicy.Minimum, QtWidgets.QSizePolicy.Expanding)
        self.gridLayout_8.addItem(spacerItem7, 3, 1, 1, 1)
        self.Activation = QtWidgets.QPushButton(self.layoutWidget)
        self.Activation.setObjectName("Activation")
        self.gridLayout_8.addWidget(self.Activation, 2, 1, 1, 1)
        spacerItem8 = QtWidgets.QSpacerItem(20, 40, QtWidgets.QSizePolicy.Minimum, QtWidgets.QSizePolicy.Expanding)
        self.gridLayout_8.addItem(spacerItem8, 5, 1, 1, 1)
        spacerItem9 = QtWidgets.QSpacerItem(40, 20, QtWidgets.QSizePolicy.Expanding, QtWidgets.QSizePolicy.Minimum)
        self.gridLayout_8.addItem(spacerItem9, 2, 0, 1, 1)
        spacerItem10 = QtWidgets.QSpacerItem(40, 20, QtWidgets.QSizePolicy.Expanding, QtWidgets.QSizePolicy.Minimum)
        self.gridLayout_8.addItem(spacerItem10, 2, 2, 1, 1)
        self.label_7 = QtWidgets.QLabel(self.layoutWidget)
        font = QtGui.QFont()
        font.setBold(True)
        font.setWeight(75)
        self.label_7.setFont(font)
        self.label_7.setAlignment(QtCore.Qt.AlignCenter)
        self.label_7.setObjectName("label_7")
        self.gridLayout_8.addWidget(self.label_7, 0, 0, 1, 3)
        self.line = QtWidgets.QFrame(self.centralwidget)
        self.line.setGeometry(QtCore.QRect(10, 120, 591, 16))
        self.line.setFrameShape(QtWidgets.QFrame.HLine)
        self.line.setFrameShadow(QtWidgets.QFrame.Sunken)
        self.line.setObjectName("line")
        self.line_3 = QtWidgets.QFrame(self.centralwidget)
        self.line_3.setGeometry(QtCore.QRect(10, 180, 591, 16))
        self.line_3.setFrameShape(QtWidgets.QFrame.HLine)
        self.line_3.setFrameShadow(QtWidgets.QFrame.Sunken)
        self.line_3.setObjectName("line_3")
        self.gridLayoutWidget_2 = QtWidgets.QWidget(self.centralwidget)
        self.gridLayoutWidget_2.setGeometry(QtCore.QRect(10, 140, 591, 41))
        self.gridLayoutWidget_2.setObjectName("gridLayoutWidget_2")
        self.gridLayout_2 = QtWidgets.QGridLayout(self.gridLayoutWidget_2)
        self.gridLayout_2.setContentsMargins(0, 0, 0, 0)
        self.gridLayout_2.setObjectName("gridLayout_2")
        self.Lancement = QtWidgets.QPushButton(self.gridLayoutWidget_2)
        self.Lancement.setObjectName("Lancement")
        self.gridLayout_2.addWidget(self.Lancement, 0, 1, 1, 1)
        self.label = QtWidgets.QLabel(self.gridLayoutWidget_2)
        self.label.setObjectName("label")
        self.gridLayout_2.addWidget(self.label, 0, 0, 1, 1)
        MainWindow.setCentralWidget(self.centralwidget)
        self.menubar = QtWidgets.QMenuBar(MainWindow)
        self.menubar.setGeometry(QtCore.QRect(0, 0, 618, 32))
        self.menubar.setObjectName("menubar")
        MainWindow.setMenuBar(self.menubar)
        self.statusbar = QtWidgets.QStatusBar(MainWindow)
        self.statusbar.setObjectName("statusbar")
        MainWindow.setStatusBar(self.statusbar)

        self.retranslateUi(MainWindow)
        QtCore.QMetaObject.connectSlotsByName(MainWindow)

    def retranslateUi(self, MainWindow):
        _translate = QtCore.QCoreApplication.translate
        MainWindow.setWindowTitle(_translate("MainWindow", "MainWindow"))
        self.label_3.setText(_translate("MainWindow", "Nombre d\'animaux"))
        self.label_4.setText(_translate("MainWindow", "Heures d\'activités"))
        self.label_5.setText(_translate("MainWindow", "Début"))
        self.label_6.setText(_translate("MainWindow", "Fin"))
        self.Animal1.setText(_translate("MainWindow", "1"))
        self.Animal2.setText(_translate("MainWindow", "2"))
        self.Animal3.setText(_translate("MainWindow", "3"))
        self.Viderpoubelle.setText(_translate("MainWindow", "Vider poubelle"))
        self.Nettoyage.setText(_translate("MainWindow", "Nettoyage"))
        self.label_2.setText(_translate("MainWindow", "Mode manuel de nettoyage"))
        self.Desactivation.setText(_translate("MainWindow", "Désactivation"))
        self.Activation.setText(_translate("MainWindow", "Activation"))
        self.label_7.setText(_translate("MainWindow", "Mode automatique de nettoyage"))
        self.Lancement.setText(_translate("MainWindow", "Lancement"))
        self.label.setText(_translate("MainWindow", "Armement de la cage"))


if __name__ == "__main__":
    import sys
    app = QtWidgets.QApplication(sys.argv)
    MainWindow = QtWidgets.QMainWindow()
    ui = Ui_MainWindow()
    ui.setupUi(MainWindow)
    MainWindow.show()
    sys.exit(app.exec_())

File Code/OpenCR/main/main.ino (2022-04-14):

/*
  Project:      CAGIUS
  Description:  Main of the OpenCR.
  Authors:      Florence Millette
              Aissatou
              Alexandre
              Laurie Croteau
              Natael Laroche-Latulippe
*/

// ========= Libraries ========
#include <Arduino.h>
#include <stdint.h>
#include <DynamixelWorkbench.h>
#include <vector>
#include "serialcomm_functions.hpp"
#include "motor_functions.hpp"
#include "action_functions.hpp"

// ========= Constant =========

//----------motor--------------

// ========= Enumerations =====

enum State
{
  Init,
  Off,     // attente du start de la cage
  Wait,    // en attente de message de la camera
  Washing, // cycle de nettoyage
  Trash,   // nettoyage de la poubelle, donc uniquement vis sans fin
  Test
};

// ========= Constant =========

// ========= Variables ========

enum State current_state;
String msg;       // messsage lu du Pi
int tier[2];
int ii;

// ========= Functions ========

void setup()
{
  // put your setup code here, to run once:
  comm_init();

  pinMode(1,OUTPUT);
  digitalWrite(1,HIGH);

  current_state = Init;
}

void loop()
{
  // put your main code here, to run repeatedly:
  switch (current_state)
  {
    
  case Init:
  {
    msg = get_msg();
    if (should_init(msg) == true)
    {
      init_motors_action();
      current_state = Off;
      send_msg("En attente du lancement de la cage");
      break;
    }
    break;
  }    
  case Off:
  {
    // waiting for the start signal, if received, state = Wait
    // send_msg("En attente du lancement de la cage");
    msg = get_msg();
    if (should_start(msg) == true)
    {
      send_msg("Cage armee");
      current_state = Wait;
      send_msg("En attente dinstruction");
      break;
    }
    if (msg == "TEST")
    {
      current_state = Test;
      send_msg("Mode Test");
      break;
    }

    break;
  }

  case Wait:
  {
    // Waiting for the Pi to send the instruction Wash, Trash or the stop of the cage signal
    msg = get_msg();

    // pi dit stop
    if (should_end(msg) == true)
    {
      send_msg("Cage arretee");
      current_state = Off;
      break;
    }

    // pi dit de débuter le nettoyage de ta poubelle
    if (should_trash(msg) == true)
    {
      current_state = Trash;
      break;
    }

    // statement sur la camera (envoye du pi), lecture de deux int, premier %
    // de la cage a nettoyer (convoyeur), second % de la poubelle a compresser

    // séparation du string qui est recu en deux integer entre 0 et 100
    String temporaire1 = should_wash(msg);

    String words1[3];
    int StringCount1 = 0;

    while (temporaire1.length() > 0)
    {
      int index = temporaire1.indexOf(' ');
      if (index == -1) // No space found
      {
        words1[StringCount1++] = temporaire1;
        break;
      }
      else
      {
        words1[StringCount1++] = temporaire1.substring(0, index);
        temporaire1 = temporaire1.substring(index + 1);
      }
    }

    tier[0] = words1[0].toInt();
    tier[1] = words1[1].toInt();

    if (tier[0] != 0 && tier[1] != 0)
    {
      send_msg("Nettoyage amorcé a " + String(tier[0]) + " tier de convoyeur et " + String(tier[1]) + " pourcent de poubelle"); // message feedback
      current_state = Washing;
      break;
    }

    break;
  }

  case Washing:
  {

    // nettoyage de la cage
    send_msg("Nettoyage en cours");

    // etape 1: ouverture de la trappe de la poubelle
    open_poubelle();
    // etape 2: ouverture des trapes du convoyeur
    open_trappes();
    //close_trappes();
    // etape 3: convoyeur (avec %)
    convoyeur(tier[0]);
    // etape 4: fermeture trapes du convoyeur
    close_trappes();
    //open_trappes();
    // etape 4: fermeture trape de la poubelle
    close_poubelle();
    // etape 5: compression de la litiere
    int ii = compression_litiere(tier[1]);
    // etape 6: retour de la pelle
    home_litiere(tier[1], ii);

    send_msg("Nettoyage fini");
    current_state = Wait;
    send_msg("En attente dinstruction");
    break;
  }

  case Trash:
  {
    // nettoyage de la poubelle (compression de la litiere a la limite de la boite, car utilisateur met un sac a la sortie
    send_msg("Nettoyage de la poubelle amorce");
    int ii = compression_litiere(100);

    home_litiere(100, ii);

    send_msg("Nettoyage de la poubelle fini");
    current_state = Wait;
    send_msg("En attente dinstruction");

    break;
  }
  case Test:
  {
    
    msg = get_msg();
    if (msg == "OpenTrappes")
    {
      open_trappes();
    }
    if (msg == "CloseTrappes")
    {
      close_trappes();
    }
    if (msg == "OpenPoubelle")
    {
      open_poubelle();
    }
    if (msg == "ClosePoubelle")
    {
      close_poubelle();
    }
    if (msg == "Convoyeur10")
    {
      convoyeur(1);
    }
    if (msg == "Convoyeur100")
    {
      convoyeur(3);
    }
    if (msg == "Litiere10")
    {
      ii = compression_litiere(10);
    }
    if (msg == "Litiere100")
    {
      ii = compression_litiere(100);
    }
    if (msg == "LitiereRetour10")
    {
      home_litiere(10, ii);
    }
    if (msg == "LitiereRetour100")
    {
      ii = 468;
      home_litiere(100, ii);
    } 
    if (msg == "HomePoubelle")
    {
     //home_motorAction1();
    }
    if (msg == "HomeTrappes")
    {
      //home_motorAction2();
    }
    if (msg == "ReadVis")
    {
      //read_MotorVisCurrent();
    }
    
    if (msg == "Off")
    {
      current_state = Off;
      send_msg("Cage mode Off");
      break;
    }

    
    break;
  } 
}
}

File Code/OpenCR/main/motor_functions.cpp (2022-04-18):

/*
  Project:      CAGIUS
  Description:  Function Motor
  Authors:      Florence Millette
                Aissatou
                Alexandre
                Laurie Croteau
                Natael Laroche-Latulippe
*/

#include "motor_functions.hpp"
#include <Arduino.h>



// ========= Functions ========

void init_motors(DynamixelWorkbench& motor)
{
/**
 * Initialisation des moteurs Dynamixel et sélection du mode de fonctionnemnet
 * @param { DynamixelWorkbench& } motor
 * @return { void }
 */
 const char *log = NULL;
 
 motor.init(DEVICE_NAME, 57600, &log);
 
        for (int i = 1; i <= 4; ++i)
    {
        const char* motor_name = i+"";
        uint16_t model_number = 0;
        //const char* log;
        //motor.init(motor_name, 57600, &log);

        if (i == 2)   // initialisation moteur trappes
        {
          motor.ping(MOTOR_TRAPPES_ID, &model_number, &log);
          motor.ledOn(MOTOR_TRAPPES_ID);        
          motor.torqueOff(MOTOR_TRAPPES_ID);                       
          motor.setReverseDirection(MOTOR_TRAPPES_ID);                       //setNormalDirection
          motor.jointMode(MOTOR_TRAPPES_ID, V_Trappes, 0, &log);  
          motor.torqueOn(MOTOR_TRAPPES_ID);
          Serial.println("Moteur 1 initialise (TRAPPES)");
        }
        else if (i == 1)   // initialisation moteur poubelle
        {
          motor.ping(MOTOR_POUBELLE_ID, &model_number, &log);
          motor.ledOn(MOTOR_POUBELLE_ID);   
          motor.torqueOff(MOTOR_TRAPPES_ID);                             
          motor.setNormalDirection(MOTOR_POUBELLE_ID);                 //setNormalDirection
          motor.jointMode(MOTOR_POUBELLE_ID, V_Trappes, 0, &log);
          motor.torqueOn(MOTOR_POUBELLE_ID);
          Serial.println("Moteur 2 initialise (POUBELLE)");
        }
        else if (i == 3)   // initialisation moteur convoyeur
        {
          motor.ping(MOTOR_VIS_ID, &model_number, &log);
          motor.ledOn(MOTOR_VIS_ID);   
          //motor.torqueOn(MOTOR_VIS_ID);                              
          //motor.setNormalDirection(MOTOR_VIS_ID);                 //setReverseDirection
          motor.wheelMode(MOTOR_VIS_ID,0, &log);
          Serial.println("Moteur 3 initialise (VIS)");
        }
        else if (i == 4)   // initialisation moteur poubelle
        {
          motor.ping(MOTOR_CONVOYEUR_ID, &model_number, &log);
          motor.ledOn(MOTOR_CONVOYEUR_ID);      
          //motor.torqueOn(MOTOR_CONVOYEUR_ID);                           
          //motor.setNormalDirection(MOTOR_CONVOYEUR_ID);                 //setReverseDirection
          motor.wheelMode(MOTOR_CONVOYEUR_ID,0, &log);
          Serial.println("Moteur 4 initialise (CONVOYEUR)");
        }
    }
}

bool tourne_continu_NMBTours(DynamixelWorkbench&  motor, uint8_t motor_IDs, int nmb_tours)
{
 /**
 * Fonction de rotation de moteur en continu selon le nombre de tour et vitesse de rotation
 * @param { DynamixelWorkbench& } motor
 * @param { uint8_t } motor_IDs
 * @param { int } nmb_tours
 * @return { bool }
 */
  motor.goalVelocity(motor_IDs, V_Convoyeur);
  delay(nmb_tours*TIME_PER_TROURS);           // temps que prend un tour avec la vitesse definie dans les constantes
  motor.goalVelocity(motor_IDs, 0);
  return true;
}

int tourne_continu_Torque(DynamixelWorkbench&  motor, uint8_t motor_IDs, int nmb_torque, int percent)
{
 /**
 * Fonction de rotation de moteur en continu selon le torque et le courant
 * @param { DynamixelWorkbench& } motor
 * @param { uint8_t } motor_IDs
 * @param { int } nmb_torque
 * @return { int }  ii
 */  
  motor.goalVelocity(motor_IDs, V_Poubelle);
  int ii = 0;
  const char *log = NULL;
  bool result = false;
  int32_t dataC = 0;
  int32_t dataCM = 1193;
  uint16_t model_number = 0;
  motor.ping(motor_IDs, &model_number, &log);
  delay(DELAY_POUBELLE_FREQCALCUL);
  //percent = 5; //valeur Hardcode pour la demo
  
  do {
    // statement block 
    dataC = 0;    
    result = motor.readRegister(motor_IDs, "Present_Current", &dataC, &log);
    delay(DELAY_POUBELLE_FREQCALCUL);
    
    Serial.print("I = ");
    Serial.print(UINT16_MAX-dataC);
    Serial.print(" sur ");
    Serial.print(dataCM);
    Serial.print(" ii = ");
    Serial.println(ii); 
    ii ++;  
  } while ((int32_t)(UINT16_MAX-dataC) <= (int32_t)((dataCM)*PERCENT_MAX_CURRENT) && ii <=  floor(INCREMENT_POUBELLE_MAX*((percent/100.0))));  //&& ii <=  INCREMENT_POUBELLE_MAX
  Serial.println(ii);   
  motor.goalVelocity(motor_IDs, 0);
  return ii;
}

bool tourne_continu_Torque_goBack(DynamixelWorkbench&  motor, uint8_t motor_IDs, int nmb_torque,  int percent, int ii)
{
 /**
 * Fonction de rotation de moteur en continu dans la meme sequence que la fonction en torque et courant
 * @param { DynamixelWorkbench& } motor
 * @param { uint8_t } motor_IDs
 * @param { int } nmb_torque
 * @param { int } ii
 * @return { bool }
 */

  motor.goalVelocity(motor_IDs, -V_Poubelle);
  const char *log = NULL;
  bool result = false;
  int32_t dataC = 0;
  int32_t dataCM = 1193;
  uint16_t model_number = 0;
  motor.ping(motor_IDs, &model_number, &log);
  bool SwitchActive = false;
  
  do {
    // statement block   
    dataC = 0;    
    result = motor.readRegister(motor_IDs, "Present_Current", &dataC, &log);
    delay(DELAY_POUBELLE_FREQCALCUL);
    
    Serial.print("I = ");
    Serial.print(dataC);
    Serial.print(" sur ");
    Serial.println(dataCM);
    Serial.print(" ii = ");
    Serial.println(ii); 
    ii --;  
    //SWITCH ????????
    SwitchActive = false;
    
  } while ((int32_t)(dataC) <= (int32_t)((dataCM)*0.9) && ii >= 3 && SwitchActive == false);
  
  motor.goalVelocity(motor_IDs, 0);

  return true;
}

bool tourne_Xrad_and_Stop(DynamixelWorkbench&  motor, uint8_t motor_IDs, float nmb_rad)
{
 /**
 * Fonction de rotation de moteur en position
 * @param { DynamixelWorkbench& } motor
 * @param { uint8_t } motor_IDs
 * @param { float } nmb_rad
 * @return { bool }
 */
  // position a atteindre avec position a pi/2 et nombre de pi/2 a se déplacer
  int32_t pos = PI_SUR_2*nmb_rad;

  motor.goalPosition(motor_IDs, pos); 

  if (nmb_rad == 0 &&  motor_IDs == MOTOR_POUBELLE_ID)
  {
    delay(DELAY_PI_SUR_2*2.5);
  }
  if (nmb_rad == 0 &&  motor_IDs == MOTOR_TRAPPES_ID)
  {
    delay(DELAY_PI_SUR_2*4);
  }
  
  delay(DELAY_PI_SUR_2*nmb_rad);
  Serial.println("Mouvement fini");
  
  return true;  
}

bool tourne_Xrad_ReturnPos(DynamixelWorkbench&  motor, uint8_t motor_IDs, float nmb_rad, uint8_t elmt)
{
 /**
 * Fonction de rotation de moteur retour a position home
 * @param { DynamixelWorkbench& } motor
 * @param { uint8_t } motor_IDs
 * @param { float } nmb_rad
 * @return { bool }
 */
 motor.goalPosition(motor_IDs, (int32_t)(PI_SUR_2*nmb_rad));

  Serial.println("Mouvement fini");
  if (nmb_rad == 0)
  {
    delay(DELAY_PI_SUR_2*1);
  }
  else 
  {
    delay(DELAY_PI_SUR_2*nmb_rad);
  }
  return true;  
}

void stop_motors(DynamixelWorkbench&  motor, uint8_t motor_IDs)
{

}
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

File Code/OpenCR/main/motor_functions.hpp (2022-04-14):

/*
  Project:      CAGIUS
  Description:  Header: Function Motor
  Authors:      Florence Millette
                Aissatou
                Alexandre
                Laurie Croteau
                Natael Laroche-Latulippe
*/

#ifndef motor_functions_h
#define motor_functions_h

#include <Arduino.h>
#include <stdint.h>
#include <DynamixelWorkbench.h>
#include <vector>

// ========= Constant =========

#if defined(__OPENCM904__)
#define DEVICE_NAME "3" // Dynamixel on Serial3(USART3)  <-OpenCM 485EXP
#elif defined(__OPENCR__)
#define DEVICE_NAME ""
#endif

//----------motor--------------
const uint8_t MOTOR_TRAPPES_ID = 2; 
const uint8_t MOTOR_POUBELLE_ID = 1;
const uint8_t MOTOR_CONVOYEUR_ID = 3;
const uint8_t MOTOR_VIS_ID = 4;

//----------utilisateion--------------
const uint8_t DELTA_POS = 20;
const int32_t V_Trappes = 50;     // vitesse des trappes
const int32_t V_Convoyeur = 25;   // vitesse du convoyeur
const int32_t V_Poubelle = -350;    // vitesse rotation de la vis sans fin (Vitesse maximale)
const int TIME_PER_TROURS = 5500; // temps nécessaire pour effectuer un demi tour de convoyeur
const int32_t PI_SUR_2 = 1000;          // position de pi/2 rad
const unsigned long DELAY_PI_SUR_2 = 1000;  // temps nécessaire a faire PI/2 avec vitesse des trappes
const unsigned long DELAY_CONV_10Percent = 6500;  // temps nécessaire a faire 10 pourcentde l'allé du convoyeur
const unsigned long DELAY_POUBELLE_FREQCALCUL = 1000;  // delay calcul
const int32_t HOME_TRAPPES = 0;
const int32_t HOME_POUBELLE = 0;
const int32_t ELMT_TRAPPES = 2;
const int32_t ELMT_POUBELLE = 1;
const int INCREMENT_POUBELLE_MAX = 466;

const float PERCENT_MAX_CURRENT = 0.41;

// ========= Functions prototype ========

void init_motors(DynamixelWorkbench&  motor);

bool tourne_continu_NMBTours(DynamixelWorkbench&  motor, uint8_t motor_IDs, int nmb_tours);

int tourne_continu_Torque(DynamixelWorkbench&  motor, uint8_t motor_IDs, int nmb_torque, int percent);

bool tourne_continu_Torque_goBack(DynamixelWorkbench&  motor, uint8_t motor_IDs, int nmb_tours, int percent, int ii);

bool tourne_Xrad_ReturnPos(DynamixelWorkbench&  motor, uint8_t motor_IDs, float nmb_rad, uint8_t elmt);

bool tourne_Xrad_and_Stop(DynamixelWorkbench&  motor, uint8_t motor_IDs, float nmb_rad);

void stop_motors(DynamixelWorkbench&  motor, uint8_t motor_IDs);

void readCurrent(DynamixelWorkbench&  motor, uint8_t motor_IDs);

void home_motor(DynamixelWorkbench&  motor, uint8_t motor_IDs);

#endif

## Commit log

2022-02-02 Add solidwork files
    [Cage.SLDPRT, Convoyeur.SLDPRT, PoubelleV2.SLDPRT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]
2022-02-12 Communication cote OpenCR
    fichier main (Arduino) avec un cpp et hpp pour les fonctions de com, ajout de switch case pour u debut de prog avec les etats de la cage
2022-02-12 Ajout de README et creation du folder PiQt pour HMI
2022-02-15 Initialisation du code pour la détection d'objet avec le Pi
2022-02-16 pages Qt de linterface pour la main window et le popu up de nettoyage
2022-02-19 transfert des fichiers .ui en .py
2022-02-19 ouverture des fenetres en py
2022-02-19 mise a jours de linterface
2022-02-20 repositionnement de la doc
    je me suis trompee de README, le tout a ete mis a la bonne place la
2022-02-21 Update README.md
    Ça ben l'air que open source est dans le larousse et que sa ce traduit pas par source ouverte. En tous cas, c'est ce que j'ai trouvé. À VÉRIFIER !!!
2022-02-21 Update README.md
    Installation de OpenCV
2022-02-21 Ajout de nouveaux fichiers de codes et des images
2022-02-22 doc de qt design
2022-03-04 Ajout de la détection des zones souillées
2022-03-05 Ajout du calcul de la zone la plus loin de la poubelle
2022-03-08 librairies et fichiers de moteurs openCR
2022-03-09 prog des moteurs
    note, referer les livrairies un peu partout est utile sinon ca compile vrm pas idk why arduino fait ca
2022-03-09 creation de header et fichier pour les fonctions d'action
    fonction de nettoyage etc
2022-03-09 analyse du message de nettoyage du pi
2022-03-09 prototype de fonction des actions
2022-03-13 Connexion des deux fenetres et debut main
2022-03-15 initialisation des moteurs avec leurs modes
2022-03-16 ajout de prototype de fonction pour les moteurs de trapes fonctionnant en radian
2022-03-16 Ajout de la license dans le README principal
2022-03-16 fonction de position de moteurs des trappes (Alle)
2022-03-16 fonction de retour position home trappes (Retour)
2022-03-16 redefinition de l'objet dyna
2022-03-16 Separation des fichiers
2022-03-16 Calibration du fishEye
2022-03-21 Fonction des moteurs trappes fonctionnel et testé
2022-03-21 vitesse et délai des moteurs 1 et 2 ajustés
2022-03-21 Fonction vitesse fonctionnelle
    Note: il va falloir trouver les valeurs des constantes, nmb de tours pour 10% et temps pour un tour a la vitesse du convoyeur
2022-03-22 ajout /tat de nettoyage de poubelle avec deuxieme pourcentage en parametre
2022-03-22 ajustement de l'indentation
2022-03-23 changement des ID des moteurs
2022-03-23 Avancement de la machine à etat
2022-03-26 debut fonction torque
    voir si la librairie est suffisante
2022-03-27 Ajout de la recherche d'ancrage et préparation pour comm
2022-03-30 Avancement de la machine à états
2022-04-03 mise a jours de la documentation OpenCr
2022-04-03 fichier source des figures
2022-04-03 fichier drawio flowchart code entier
2022-04-04 Ajout GPIO et correction détection
    [FonctionsCam.py]
2022-04-04 Ajout CAD Caméra
2022-04-04 Étapes Calibration
2022-04-04 Ajout grille de calibration
2022-04-04 Nétoyage code Calibration
2022-04-05 torque off avant counterclockwise
2022-04-06 Commentaires et nettoyage des fichiers
2022-04-09 Commentaires et séparation des fichiers
2022-04-09 lecture de I
2022-04-10 Poubelle Home
    voir si on ajoute une switch
    il restera a ajuster les variables pour pas briser la cage (courrant)
2022-04-11 mise a jour du flowchart communication
2022-04-12 Finition code Camera
2022-04-12 Ajout Thread
2022-04-12 Implemetation de lecture de courrant Alle
2022-04-12 Implementation du retour de la vis
2022-04-13 Resize image camera
2022-04-13 ajustement de constantes
2022-04-13 valeur de demo hardcode
2022-04-14 Update flowchart
2022-04-14 png flowchart
2022-04-14 liens vers les images
2022-04-14 changement image flowchart
2022-04-14 images de la cage ajoutee
2022-04-18 retrait de ligne hardcode demo
